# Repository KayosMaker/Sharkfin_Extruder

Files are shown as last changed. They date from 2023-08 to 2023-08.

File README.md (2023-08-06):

# Sharkfin Extruder
Sharkfin is a lightweight BMG gear based extruder, which uses the Sherpa Mini mounting standard.  This extruder is based on [Sailfin](https://github.com/CroXY3D/Sailfin-Extruder), and the license carries over from there. Sharkfin is made to work in the Voron Printer ecosystem, and draws on that pool of standard parts. It can use standard BMG extruder components, as well as the new RIDGA one piece gear from BMG(my preference). There is an optional front piece with the added mounting ear(shown below), compatible with the [XOL Toolhead](https://github.com/Armchair-Engineering/Xol-Toolhead).  
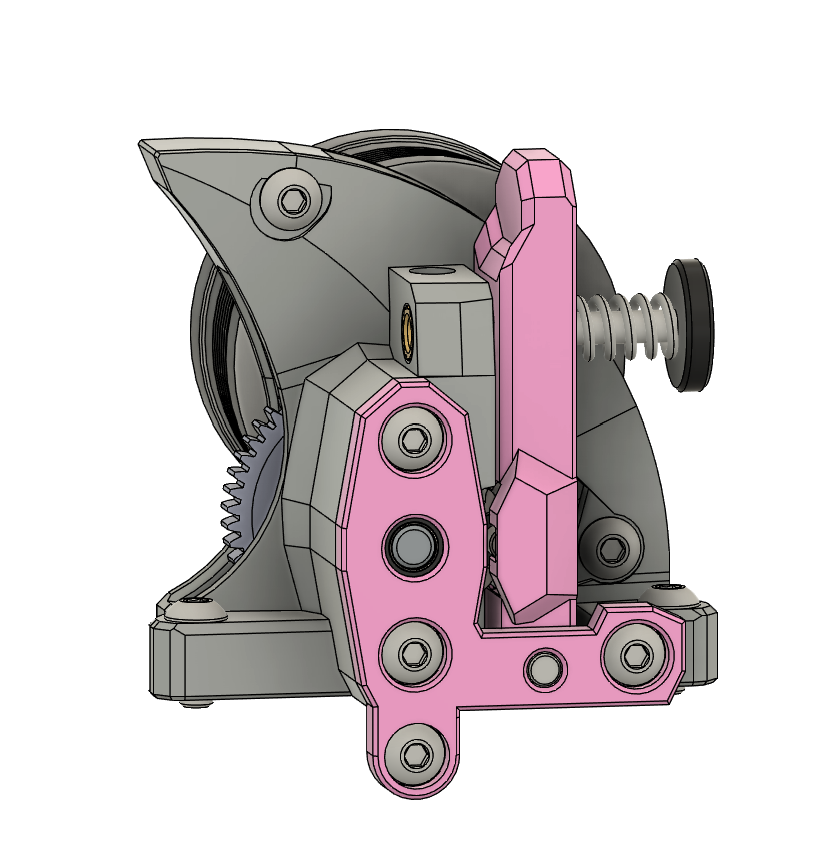
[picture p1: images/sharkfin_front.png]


## What's New
Compared to Sailfin and old Sharkfin, the geometry is fully reworked, inside and out.  On the inside, space was made to install RIDGA, while simultaneously tightening up clearances around the filament path.  I retweaked everything to line up properly with 0.2mm layers(more of a headache than I would have ever expected, due to my own shoddy old work). I also now have a built in support around the filament path. This leads to a much more cleanly printed opening around the drive gears. As for the new exterior look(aka "Stealthfin"), I absolutely asked for outside help.  The mod master himself, @hartk1213, came to my rescue and did a complete stealthification of the sharkfin look.  I then used his work as inspiration for the version you see here.  I outright stole a lot of his lines, and altered some to better suit my own taste.  The result looks pretty darn cool, more due to his work than mine.  Thanks buddy!
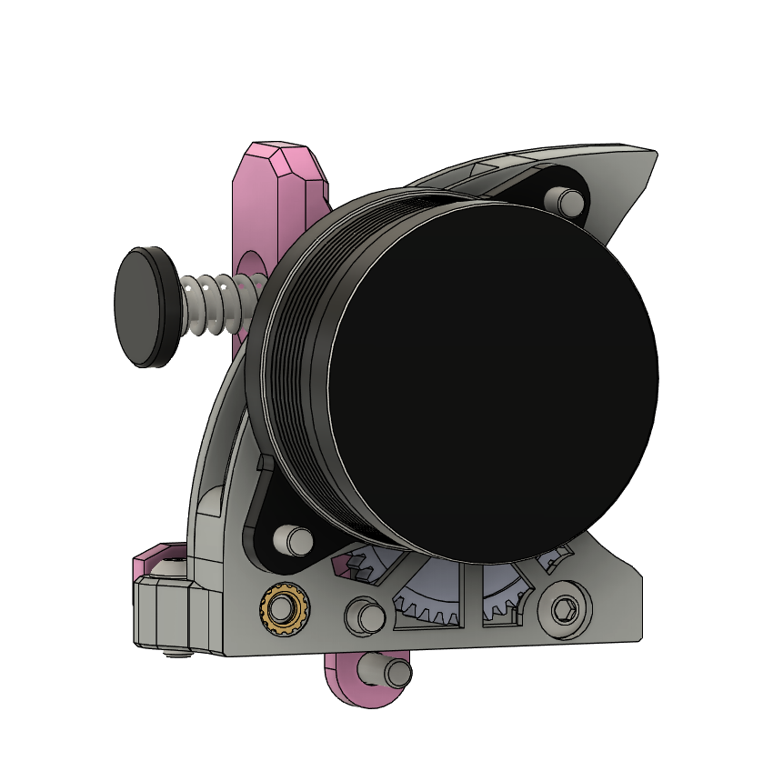
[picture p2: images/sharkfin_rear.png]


## Idler Arms
The three tension arm idler options are shown below.  Both smooth idlers are centered on the filament.  This means the single bearing will press flat against the filament, and the dual bearing will press the line between the two against the filament. The bearings are held captive laterally with both designs, but spin freely on their 5mm shafts as the filament feeds. These are experimental, and it's currently unclear if there will be a difference between the two.  They may help with "issue 6", if it's coming from runout on the drive gear, or backlash between the two drive gears.  I prefer to use RIDGA with a standard idler gear for maximum push.  The smooth idlers are simply an option. Please let me know if you try them and have any feedback!  
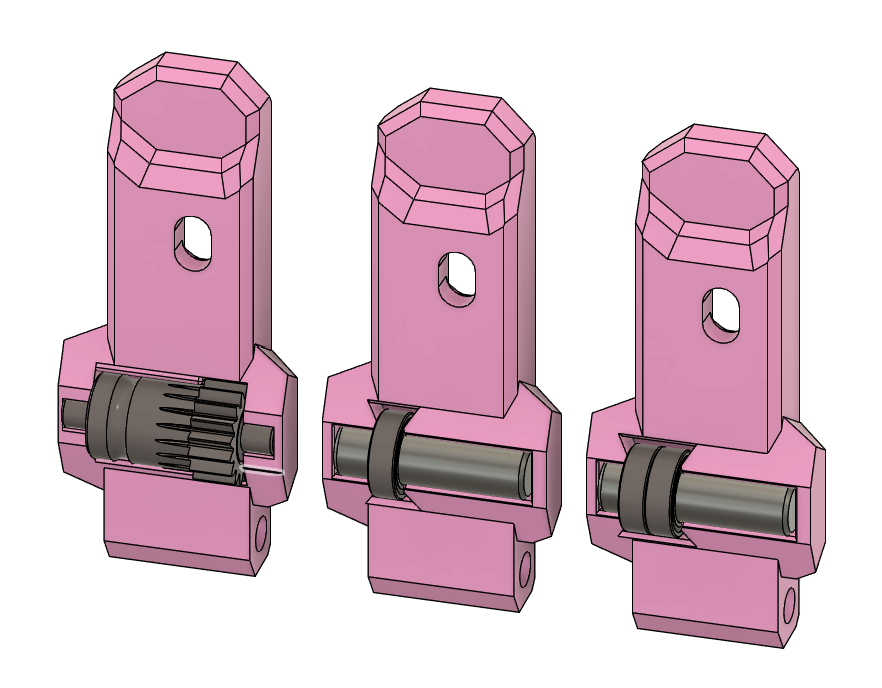
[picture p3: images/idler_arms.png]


## Built in Support
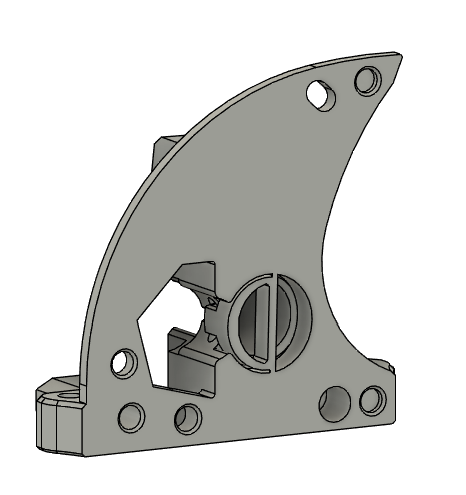
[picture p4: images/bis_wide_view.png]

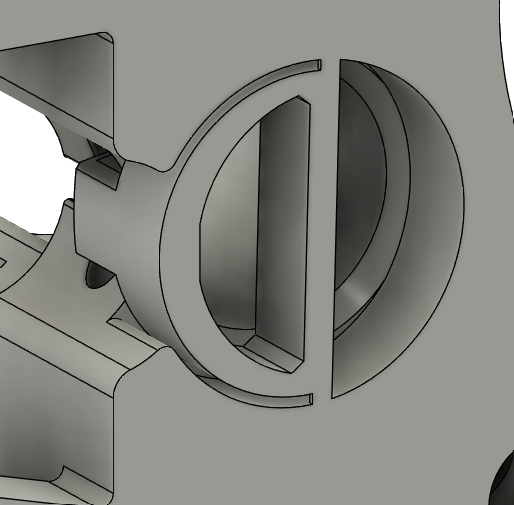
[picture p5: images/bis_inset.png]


As mentioned above, this extruder includes built in support around the opening in the filament path.  These images show the support and where to manipulate it.  The two .4mm bridges circled in red need to be cut with side cutters or a knife.  They are placed where you can't hurt anything if u mar the surrounding plastic.  Once the little bridges are cut, the support piece is mostly free.  With a pair of needle nose pliers, grab the support at the spot circled in yellow.  Give a gentle twisting motion around the axis of the filament path, and the support should come right out. If it doesn't come out easily, your extrusion multiplier may be too high.  Once the support is out, I like to carefully run a 2mm drillbit through the filament path from both sides.

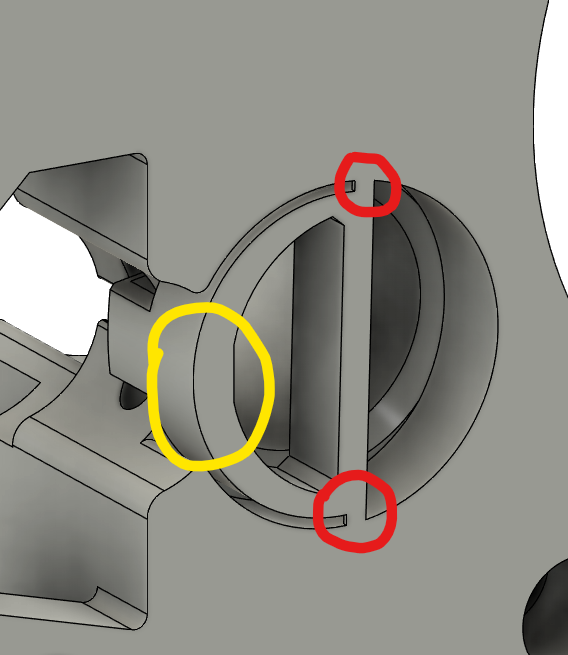
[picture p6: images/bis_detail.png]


## BOM
To build your own Sharkfin, you will need the following, in addition to the printed parts.
* NEMA14 36mm Stepper Motor with 8, 9, or 10 tooth spur gear
* BMG Extruder Components kit:
  * Bondtech BMG Drive Gears Kit
  * Bondtech Shaft/Gear Assembly, with set screw
  * BMG Thumbscrew/spring/washer
  * 3mmx30 pin (idler arm pivot)
  * 3mmx20 pin  (idler shaft)
  * 2 - 5x8x2.5 bearings
* 1 - 0.5mm M5 shim
* 5 - M3x5x4 Heatsets (standard Voron heatsets)
* 1 - M3x25 BHCS
* 2 - M3x16 BHCS
* 3 - M3x8 BHCS
* 2 - M3x10 BHCS
* Optional Components for Smooth Idler:
  * 1 or 2 - 5x8x2.5 bearings (standard BMG internals bearings)
  * M5 shaft (anything from 10-18mm long will do)

## What to Print
Every Sharkfin is made up of 4 printed parts: The Front, Mid, Rear, and the Thumb Lever.  Optional parts are the Front with Ear(for Xol Toolhead and possibly K3), and the 2 optional Smooth Idler Thumb Levers(experimental YMMV).  All STL's are oriented correctly for printing.  Use standard Voron parts settings for printing.  Sharkfin is designed for ABS or ASA.

## Heatsets
There are 5 heatserts that need to be installed.  The first 4 are all in the Mid body, as shown.

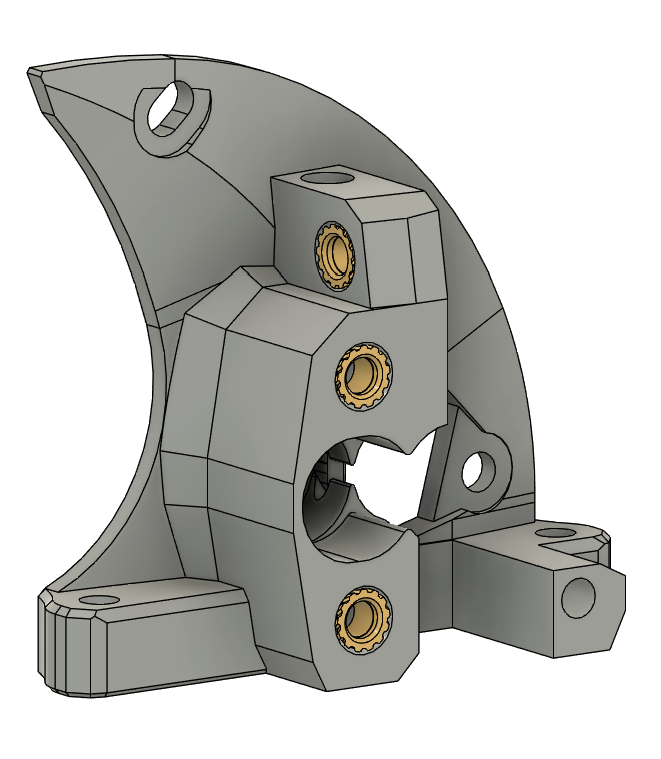
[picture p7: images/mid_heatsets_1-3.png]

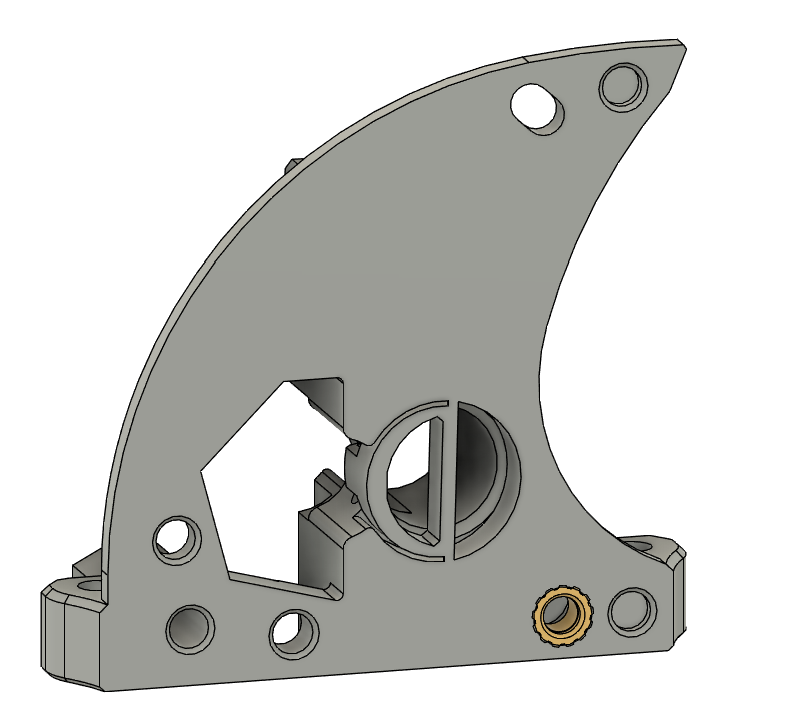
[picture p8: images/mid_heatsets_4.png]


The last heatset goes in the Rear body:

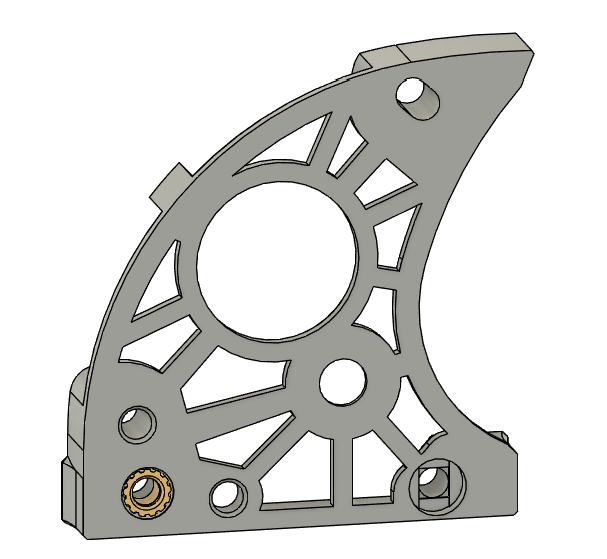
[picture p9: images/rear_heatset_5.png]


## Build
The build should be fairly self explanatory, based on the parts and pictures.  The build up for the BMG drive stack, from the front, is: bearing,0.5mm shim,drive gear, 50t gear, bearing.  Don't forget the shim.  It aligns the drive gear properly with the filament path.  RIDGA also needs the 0.5mm shim.  The 3mm pin for the Thumb lever pivot will be a couple mm too long.  I usually leave the extra hanging out the back of the extruder, since it intereferes with nothing and cant be seen there.  If you have any feedback for Sharkfin feel free to open an issue, or dm me on discord.  

## Usermods
Mod|Description|Link
|:--------:|:-------------------------:|:-----------------:|
StackingDeez Destealthed Sharkfin Light|Currently experimental destealthed and lightened version of Sharkfin| [Sharkfin Light](usermods/StackingDeezLayers/)

## Thanks
Thanks to Ocho Camino for an awesome extruder to build on.

Also thanks to the Annex guys for kicking so much ass on the Sherpa extruders.  Those things are so refined and stripped down to the essentials, I didnt even feel any urge to try and compete with em(cause u cant improve on em for compact light bmg extruders really, at least i couldnt).  Instead I could lean into my own love of overkill, without worrying about the weight of this thing.  Sherpa also provides the mount I'm using, so another nod to that!

Thanks again to Hartk for taking the time to help with this.  If it wasnt for his help and advice, I wouldnt even be making parts.

Thanks to Clee for everything here.  He introduced me to Sailfin.  He convinced me to rework it for Voron Heatserts.  He even convinced me to keep the point that led to it becoming Sharkfin, where I would have snubbed it.  Style points all round.  Thanks mate!

## Links
Old Sharkfin and Sailfin for Voron Heatserts still live on [my fork of Sailfin](https://github.com/KayosMaker/Sailfin-Extruder).

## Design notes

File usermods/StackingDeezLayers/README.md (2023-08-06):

## Sharkfin light

Modded version of Sharkfin Stealthfin that is lighter, and no longer is "stealthy". I added cutouts, re-worked the OG Sharkfin thumb lever and added that, removed some plastic at the bottom too

I included CAD, but not STLs. I do not recommend printing this (yet), as there is probably issues.

Edit: Kayos here.  I added STLS.  Play at your own risk. :D



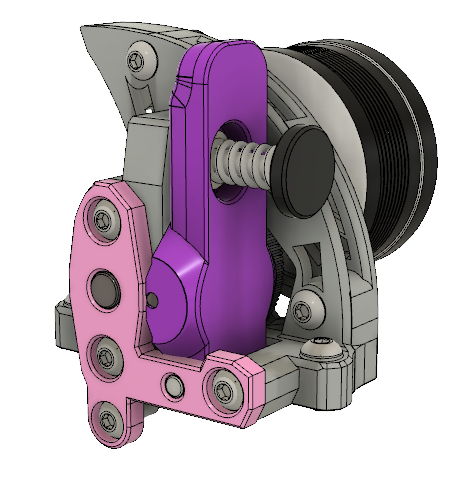
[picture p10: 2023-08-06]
usermods/StackingDeezLayers/Images/side2.png

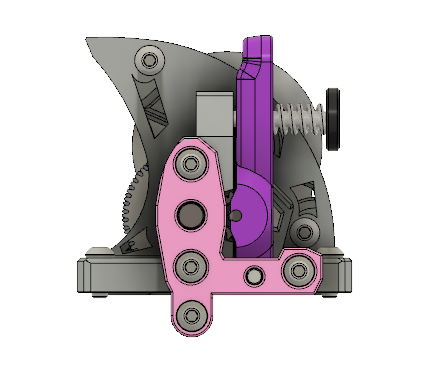
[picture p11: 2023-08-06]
usermods/StackingDeezLayers/Images/front.png

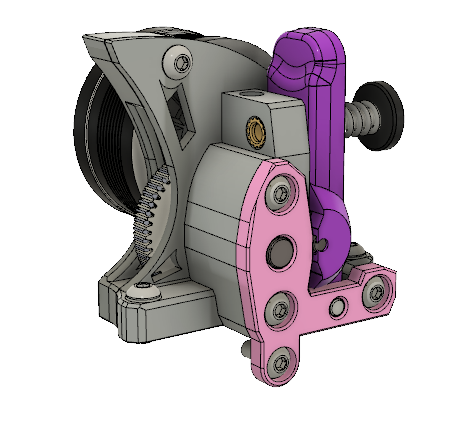
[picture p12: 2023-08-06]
usermods/StackingDeezLayers/Images/side1.png

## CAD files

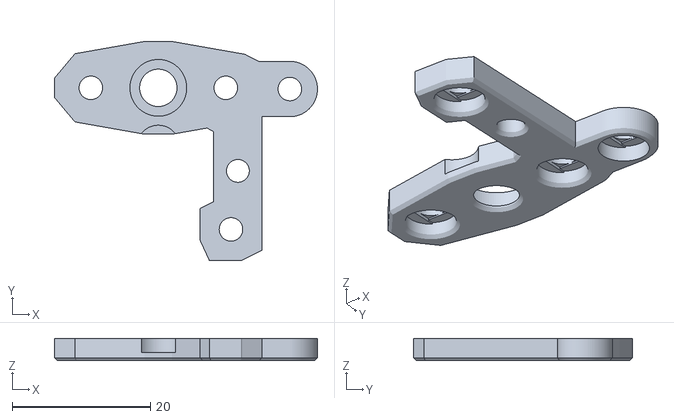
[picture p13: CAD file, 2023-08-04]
STLs/Front_with_Ear.stl
38.0 x 31.7 x 3.20

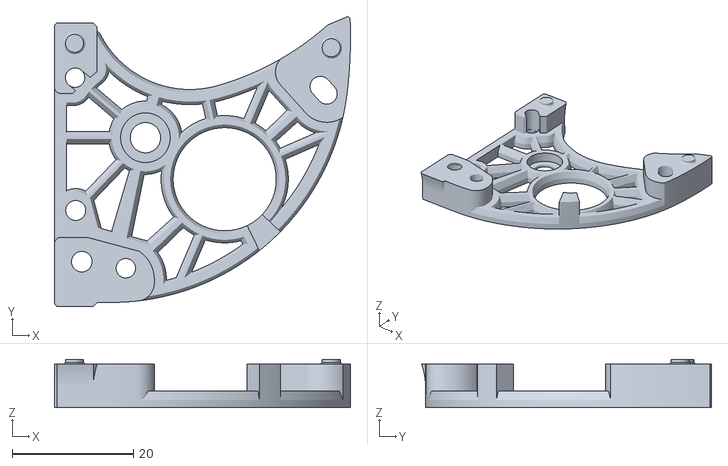
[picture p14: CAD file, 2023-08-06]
usermods/StackingDeezLayers/STLs/Rear.stl
48.8 x 47.8 x 8.00

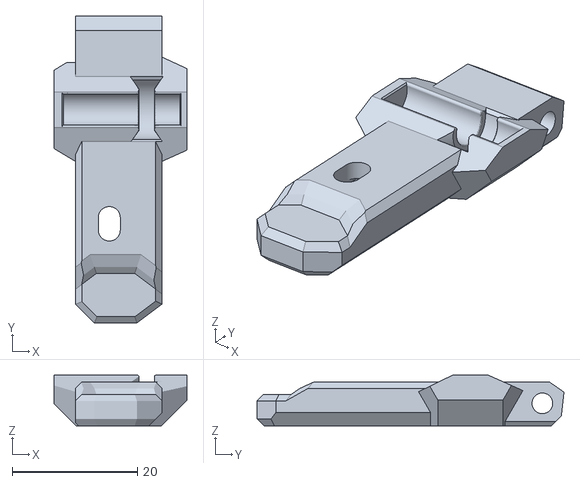
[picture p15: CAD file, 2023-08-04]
STLs/thumb lever smooth idler single bearing.stl
21.2 x 49.1 x 8.10

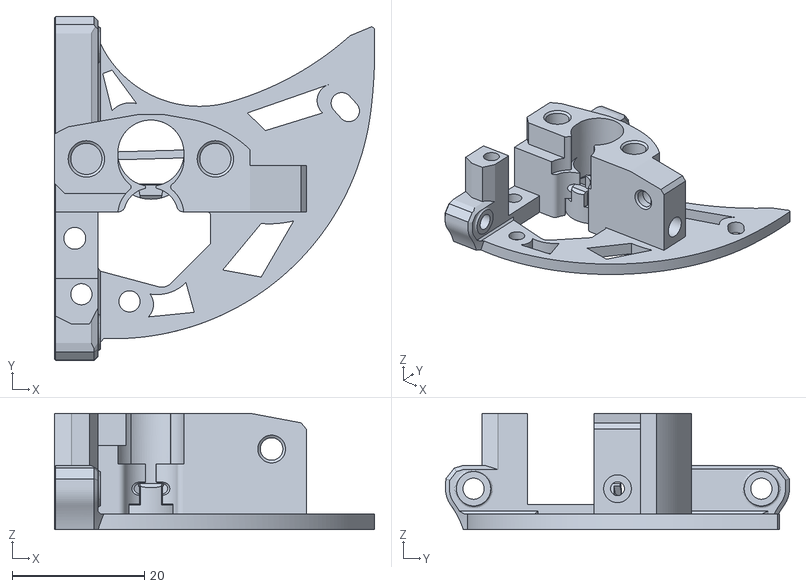
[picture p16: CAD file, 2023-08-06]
usermods/StackingDeezLayers/STLs/Mid.stl
48.4 x 52.0 x 17.6

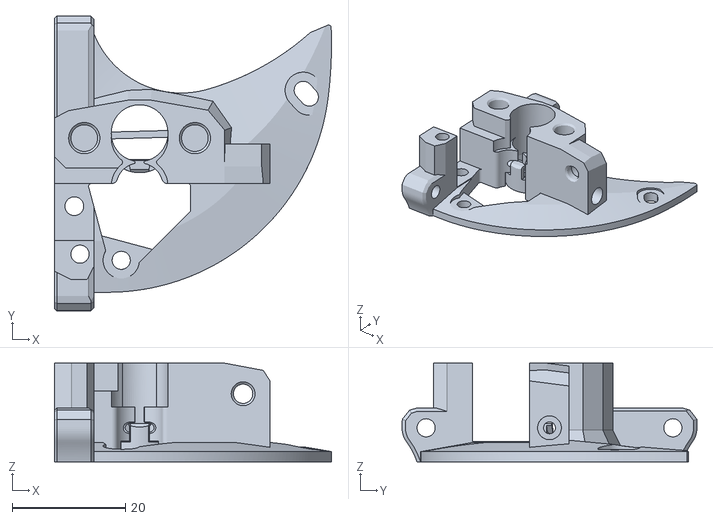
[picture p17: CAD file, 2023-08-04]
STLs/Mid.stl
48.8 x 52.0 x 17.4

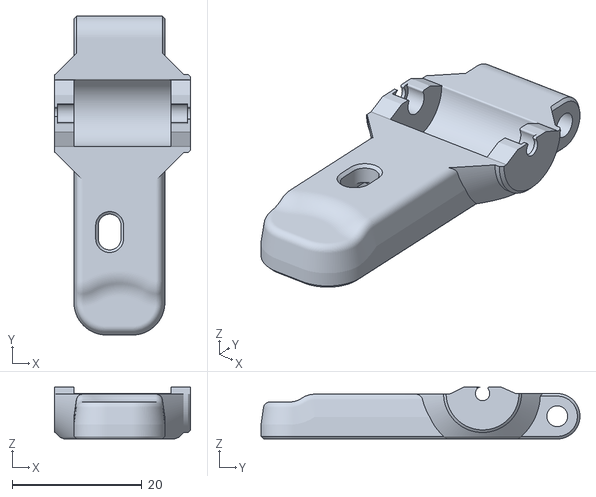
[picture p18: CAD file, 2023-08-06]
usermods/StackingDeezLayers/STLs/thumb lever.stl
21.0 x 49.1 x 8.00

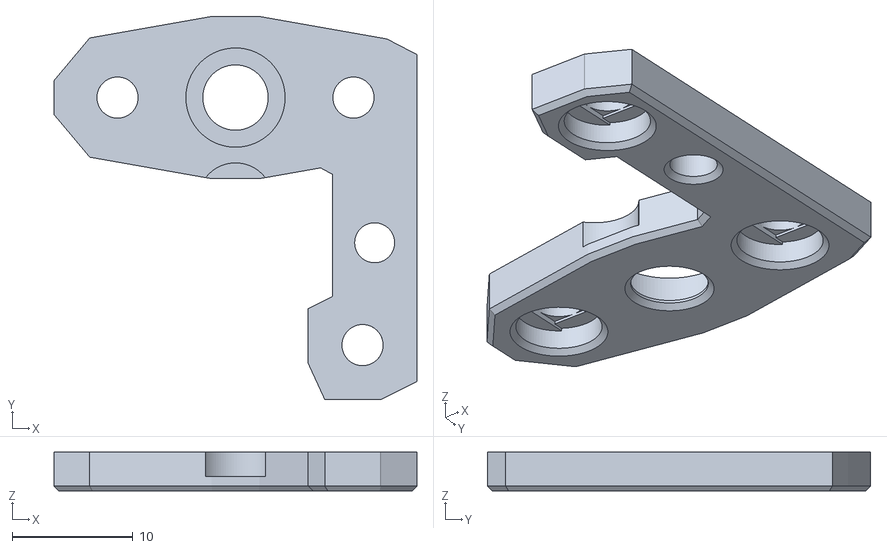
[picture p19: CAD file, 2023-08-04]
STLs/Front.stl
30.0 x 31.7 x 3.20

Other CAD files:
STLs/Rear.stl
usermods/StackingDeezLayers/STLs/Front with Ear.stl
STLs/thumb lever smooth idler double bearing.stl
STLs/thumb lever bmg gear.stl

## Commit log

2023-08-04 add heatset pics
2023-08-04 add stls
    [Front.stl, Front_with_Ear.stl, Mid.stl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]
2023-08-04 add cad
2023-08-06 add stls for sdeez usermod
    [Front with Ear.stl, Mid.stl, Rear.stl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]
2023-08-06 jumping through hoops to change the case of a foldername
    [Front with Ear.stl, Mid.stl, Rear.stl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]
2023-08-06 jumping through hoops to change the case of a foldername again
    [Front with Ear.stl, Mid.stl, Rear.stl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]
